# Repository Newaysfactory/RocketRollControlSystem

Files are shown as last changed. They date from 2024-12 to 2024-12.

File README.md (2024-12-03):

# RocketRollControlSystem
Repository containing code, documentation and other about my master's degree thesis about an aerodynamic roll control system for model rockets 

## Things to know before you start
* Main source of documentation is my degree thesis placed on the repository root folder.
* This source code and documentation is from 2012. It is provided essentially for educational purposes, since many of the hardware components used are obsolete today.
* Documentation and the master's degree thesis are mainly in italian.

## What you find here
* **Thesis_2.3.pdf** Start [here](https://github.com/Newaysfactory/RocketRollControlSystem/blob/036ea757c4abbbe03a6e53f3893280afd1d1502c/Thesis_2.3%20-%20Active%20roll%20control%20system%20for%20a%20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))  to understand this project
* **License** This project is under GNU General Public License v3.0
* **FlightTrialsLogbook** Logbook of the six experimental fligts I did with the roll control system
* **Electronics -> Firmware** The source code of the roll control system in C language. Open it with Microchip MPLAB IDE. Under "File per MPLAB Simulator" it also contains some stimuli file I used to test the system on bench
* **Electronics -> HardwareDesign** The PCB images (top and bottom) and the schematic and PCB source. To open in Labcenter Proteus ISIS and ARES. Further info in the local readme.txt
* **ExcelSheets** Some spreadsheets I used to dimension the control fins. Further info in the local readme.txt
* **Matlab** A couple of Simulink models I used to design the control system. Those closed loop models contains the mathematical model of the rocket, the actuator dynamics, the fins aerodynamics and the controller. Further info in the local readme.txt
* **Openrocket** The .ENG rocket motor thrust curves to be used with RockSim
* **PC Software** The source code in Visual Basic and the executable of the software I developed to setup the roll control system and to download flight data after the flight. Further info in the local readme.txt
* **Pictures** Pictures of all the building process
* **Rocket drawings** 3D CAD mechanical drawings of the rocket and of the control system in McNeel Rhinoceros format
* **RocksimModel** Rocksim model to simulate the rocket stability and simulate the flight

## Known issues and limitations:
* Roll angle, rate and acceleration in output from the roll Kalman fileter are not fully coherent. I never investigate further.

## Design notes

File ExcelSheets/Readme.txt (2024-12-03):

Folder content

Analisi dati di volo - Prova a terra per integrazione.xlsx
I did a ground recording moving the rocket and tried to replicate in excel the same integration algorithm is running on the microcontroller

Output Digital DATCOM.xlsx
Spreadsheet summarizing the output of the digital DATCOM fortran software for my control fins

Dimensionamento canard per tentativi.xlsm
Spreadsheet with a Macro to find the canard fins dimension given some input data 

Momento di cerniera.xlsx
A spreadsheet to calculate the hinge torque depending on the fin geometry, alpha (rocket angle of attack) and delta (fin deflection)

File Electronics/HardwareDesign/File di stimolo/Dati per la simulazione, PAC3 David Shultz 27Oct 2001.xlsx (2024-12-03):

*** Conf | iguration | ***
Trigger: | G-switch,
Smart Re | covery opt | ion enabl
Timed re | covery set | at 25 se
Data is | sampled at | 200 Hz
Inputs t | hat were s | ampled: A
This dat | a was gene | rated wit
and down | loaded fro | m an RDAS
 |  |  |  |  |  |  | 0 m/s^2 (V) = |  | 0 m = V0 = |  | 0 m/s^2 (V) = |  |  | 0 m = V0 =
*** Inte | rpreted da | ta *** |  |  |  |  | 2.41 |  | 4.085 |  | 1974.3 |  |  | 3346
Time | Acc [G] | Alt [ft] | Time | Acc [m/s^2] | Alt [m] | Time | Acc [V] | Time | Alt [V] | Time | Acc [ADC] |  | Time | Alt [ADC]
-2.000 | 1.10 | -7 | 0.000 | 10.791 | -2.1336 | 0.000 | 2.366 | 0.000 | 4.086212722 | 0.000 |  |  | 0.000 | 3347
-1.995 | 1.00 | -7 | 0.005 | 9.81 | -2.1336 | 0.005 | 2.37 | 0.005 | 4.086212722 | 0.005 |  |  | 0.005 | 3347
-1.990 | 1.00 | -7 | 0.010 | 9.81 | -2.1336 | 0.010 | 2.37 | 0.010 | 4.086212722 | 0.010 |  |  | 0.010 | 3347
-1.985 | 0.90 | 18 | 0.015 | 8.829 | 5.4864 | 0.015 | 2.374 | 0.015 | 4.081882785 | 0.015 |  |  | 0.015 | 3344
-1.980 | 1.00 | -7 | 0.020 | 9.81 | -2.1336 | 0.020 | 2.37 | 0.020 | 4.086212722 | 0.020 |  |  | 0.020 | 3347
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

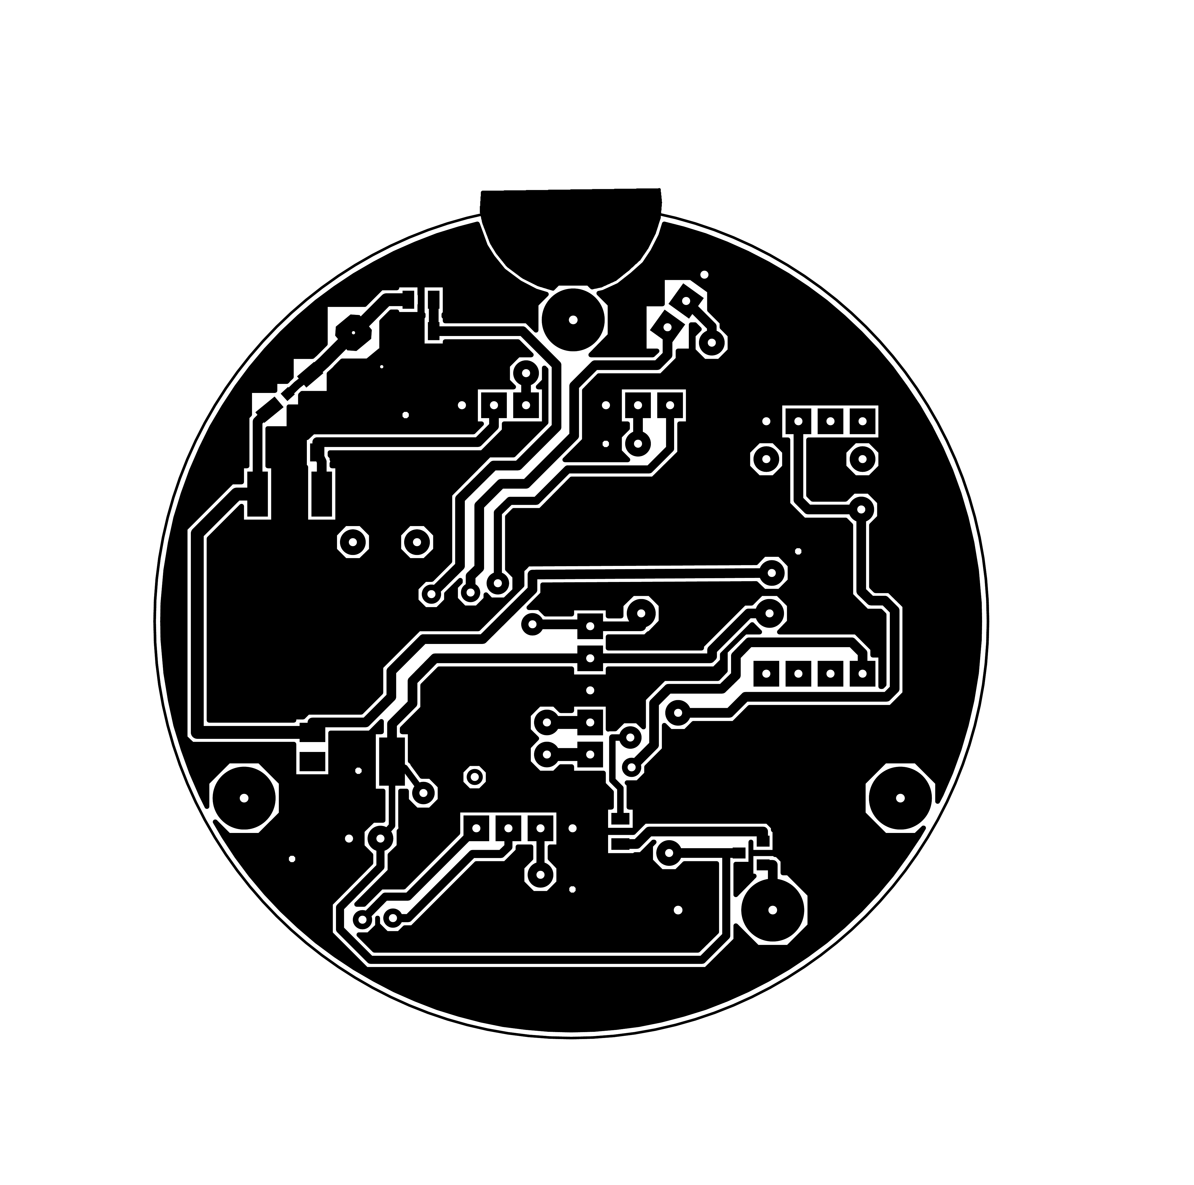
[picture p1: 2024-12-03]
Electronics/HardwareDesign/pcb scheda madre bottom.tif

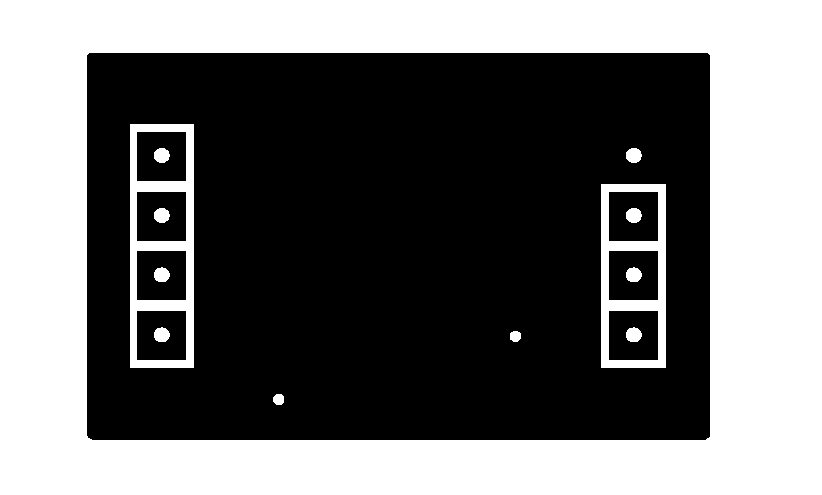
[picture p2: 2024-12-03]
Electronics/HardwareDesign/pcb gyro bottom.tif

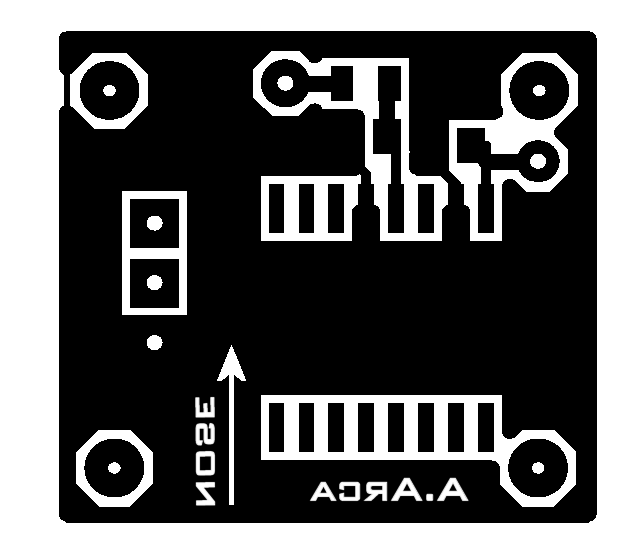
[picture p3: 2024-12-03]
Electronics/HardwareDesign/pcb accelerometro top.tif

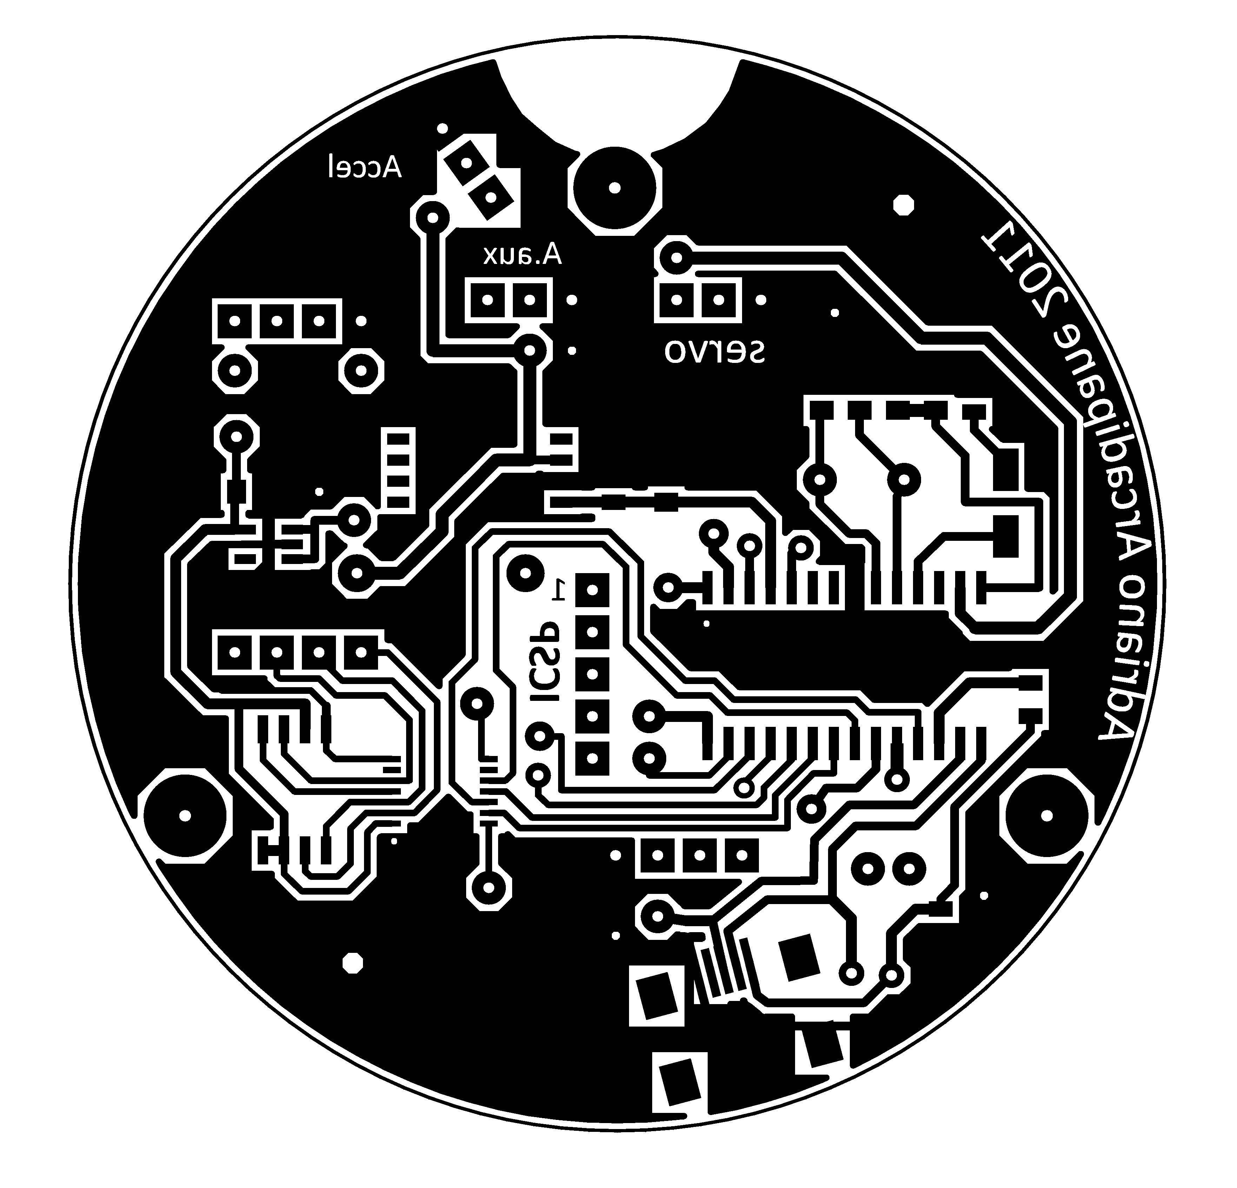
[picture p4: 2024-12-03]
Electronics/HardwareDesign/pcb scheda madre top.tif

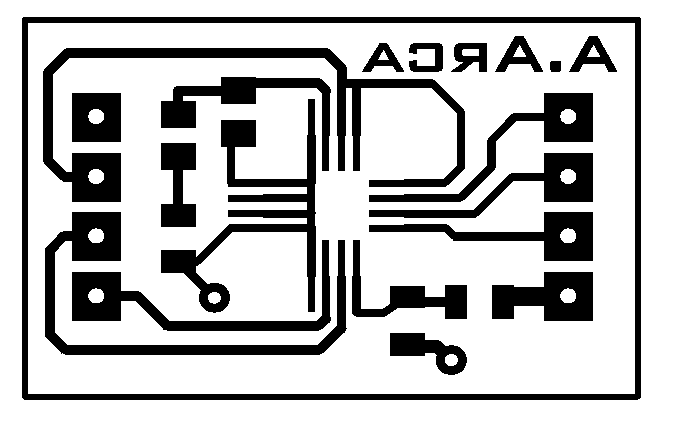
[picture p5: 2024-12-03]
Electronics/HardwareDesign/pcb gyro top.tif

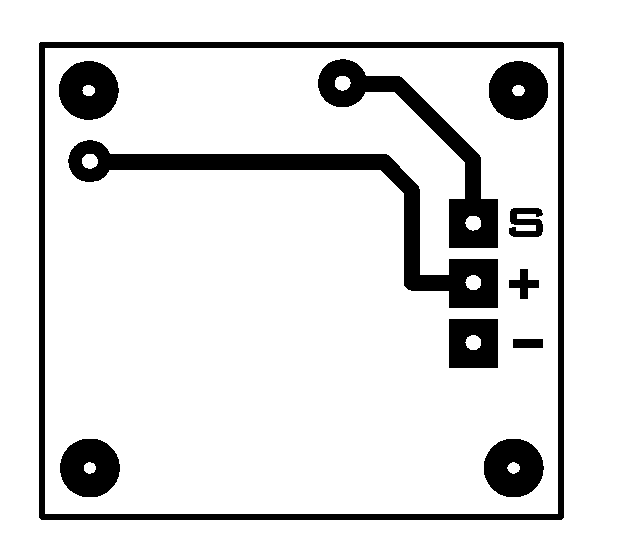
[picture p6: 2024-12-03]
Electronics/HardwareDesign/pcb accelerometro bottom.tif

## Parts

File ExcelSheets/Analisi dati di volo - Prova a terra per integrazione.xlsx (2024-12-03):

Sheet: Dati tabulari
 |  |  |  |  |  | Volo1 |  |  |  |  |  |  |  |  |  |  |  |  | Integrato con metodo dei trapezi
T | Acc | P | Aux | GyroX(-yaw) | GyroY(Pitch) | GYroZ(Roll) | Alt | Speed | Acc | Ang p | Ang speed | Ang acc | Servo pos | Yaw v (-X) | Pitch v (Y) | Roll v (Z) | Roll v (filtered) | pitch angle | Yaw angle | Roll angle | Roll angle (filtered)
[s] | [ADC] | [ADC] | [ADC] | [ADC] | [ADC] | [ADC] | [m] | [m/s] | [m/s^2] | [rad] | [rad/s] | [rad/s^2] | [rad] | [deg/s] | [deg/s] | [deg/s] | [deg/s] | [deg] | [deg] | [deg] | [deg]
0 | 2005 | 3325 | 3061 | 3 | 101 | 2832 | 0.4 | 9.14 | 11.24 | 0 | 0.378 | 0000,00 0,00000 |  | -0.0525 | 1.7675 | 49.9625 | 21.6594 | -0.0076125 | 0.0126875 | 0.5158125 | 0.2432385
0.01 | 2001 | 3324 | 3060 | 84 | 44 | 3017 | 0.55 | 9.3 | 11.27 | 0 | 0.471 | 0000,00 0,00000 |  | -1.47 | 0.77 | 53.2 | 26.9883 | -0.0102375 | 0.015575 | 1.0616375 | 0.539193
0.02 | 2002 | 3326 | 3060 | -54 | -11 | 3175 | 0.54 | 9.34 | 11.23 | 0 | 0.562 | 0000,00 0,00000 |  | 0.945 | -0.1925 | 55.965 | 32.2026 | -0.007875 | 0.0163625 | 1.6538375 | 0.889296
0.03 | 2003 | 3325 | 3062 | 27 | 20 | 3547 | 0.61 | 9.43 | 11.15 | 0 | 0.66 | 0000,00 0,00000 |  | -0.4725 | 0.35 | 62.475 | 37.818 | -0.0048125 | 0.0168875 | 2.32925 | 1.2998505
0.04 | 2006 | 3326 | 3059 | -62 | -14 | 4126 | 0.6 | 9.45 | 10.91 | 0 | 0.773 | 0000,00 0,00000 |  | 1.085 | -0.245 | 72.6075 | 44.2929 | -0.0051625 | 0.016275 | 3.078425 | 1.7748675
0.05 | 1998 | 3326 | 3061 | 66 | 7 | 4390 | 0.59 | 9.49 | 11.16 | 0 | 0.885 | 0000,00 0,00000 |  | -1.155 | 0.1225 | 77.2275 | 50.7105 | -0.015225 | 0.0114625 | 3.87345 | 2.314347
0.06 | 1996 | 3326 | 3059 | 49 | -62 | 4650 | 0.58 | 9.53 | 11.48 | 0 | 0.998 | 0000,00 0,00000 |  | -0.8575 | -1.085 | 81.7775 | 57.1854 | -0.0105875 | 0.0140875 | 4.6855375 | 2.9145645
0.07 | 1987 | 3326 | 3060 | -102 | 92 | 4585 | 0.58 | 9.6 | 12.25 | 0 | 1.097 | 0000,00 0,00000 |  | 1.785 | 1.61 | 80.64 | 62.8581 | 0.002975 | -0.0037625 | 5.0033375 | 3.504468
0.08 | 2006 | 3326 | 3060 | -53 | -296 | -999 | 0.57 | 9.62 | 11.8 | 0 | 0.962 | 0000,00 0,00000 |  | 0.9275 | -5.18 | -17.08 | 55.1226 | 0.0090125 | -0.0546875 | 4.9116375 | 4.028763
0.09 | 2002 | 3326 | 3060 | -16 | -286 | -95 | 0.56 | 9.66 | 11.67 | 0 | 0.868 | 0000,00 0,00000 |  | 0.28 | -5.005 | -1.26 | 49.7364 | 0.0126 | -0.071575 | 4.902275 | 4.5012015
0.1 | 1998 | 3326 | 3061 | -25 | 93 | -58 | 0.56 | 9.7 | 11.78 | 0 | 0.781 | 0000,00 0,00000 |  | 0.4375 | 1.6275 | -0.6125 | 44.7513 | 0.014175 | -0.0441 | 4.8580875 | 4.919778
0.11 | 2000 | 3326 | 3061 | 7 | 221 | -493 | 0.55 | 9.74 | 11.76 | 0 | 0.68 | 0000,00 0,00000 |  | -0.1225 | 3.8675 | -8.225 | 38.964 | 0.014875 | -0.01295 | 4.78555 | 5.2833465
0.12 | 1998 | 3326 | 3060 | -15 | 135 | -382 | 0.55 | 9.78 | 11.86 | 0 | 0.589 | 0000,00 0,00000 |  | 0.2625 | 2.3625 | -6.2825 | 33.7497 | 0.0216125 | 0.006475 | 4.72885 | 5.597064
0.13 | 2003 | 3325 | 3060 | -62 | 87 | -312 | 0.62 | 9.87 | 11.65 | 0 | 0.506 | 0000,00 0,00000 |  | 1.085 | 1.5225 | -5.0575 | 28.9938 | 0.02905 | 0.02065 | 4.6834375 | 5.8655145
0.14 | 2001 | 3324 | 3060 | -23 | 75 | -253 | 0.77 | 10.02 | 11.6 | 0 | 0.431 | 0000,00 0,00000 |  | 0.4025 | 1.3125 | -4.025 | 24.6963 | 0.0329 | 0.029225 | 4.63925 | 6.092136
0.15 | 2004 | 3326 | 3062 | -21 | 23 | -298 | 0.76 | 10.04 | 11.39 | 0 | 0.36 | 0000,00 0,00000 |  | 0.3675 | 0.4025 | -4.8125 | 20.628 | 0.0373625 | 0.0305375 | 4.601975 | 6.2809395
0.16 | 2007 | 3326 | 3060 | -30 | -8 | -174 | 0.75 | 10.06 | 11.05 | 0 | 0.299 | 0000,00 0,00000 |  | 0.525 | -0.14 | -2.6425 | 17.1327 | 0.041825 | 0.03115 | 4.5878875 | 6.437655
0.17 | 2006 | 3326 | 3061 | -21 | 15 | -33 | 0.74 | 10.07 | 10.83 | 0 | 0.248 | 0000,00 0,00000 |  | 0.3675 | 0.2625 | -0.175 | 14.2104 | 0.049 | 0.041475 | 4.6004 | 6.5685855
0.18 | 2000 | 3326 | 3061 | -61 | 103 | 130 | 0.73 | 10.1 | 10.99 | 0 | 0.209 | 0000,00 0,00000 |  | 1.0675 | 1.8025 | 2.6775 | 11.9757 | 0.05845 | 0.056 | 4.6249875 | 6.677742
0.19 | 2002 | 3326 | 3060 | -47 | 63 | 105 | 0.72 | 10.13 | 11.01 | 0 | 0.172 | 0000,00 0,00000 |  | 0.8225 | 1.1025 | 2.24 | 9.8556 | 0.065625 | 0.0630875 | 4.629975 | 6.764265
0.2 | 2004 | 3326 | 3060 | -35 | 18 | -94 | 0.72 | 10.15 | 10.91 | 0 | 0.13 | 0000,00 0,00000 |  | 0.6125 | 0.315 | -1.2425 | 7.449 | 0.0748125 | 0.0681625 | 4.6118625 | 6.8275815
0.21 | 2000 | 3326 | 3062 | -70 | 40 | -159 | 0.71 | 10.18 | 11.05 | 0 | 0.091 | 0000,00 0,00000 |  | 1.225 | 0.7 | -2.38 | 5.2143 | 0.085925 | 0.0721 | 4.5801 | 6.8682645
0.22 | 1996 | 3325 | 3060 | -57 | 5 | -250 | 0.78 | 10.29 | 11.39 | 0 | 0.051 | 0000,00 0,00000 |  | 0.9975 | 0.0875 | -3.9725 | 2.9223 | 0.0916125 | 0.0595 | 4.521475 | 6.8848815
0.23 | 2003 | 3326 | 3061 | -8 | -149 | -466 | 0.78 | 10.31 | 11.28 | 0 | 0.007 | 0000,00 0,00000 |  | 0.14 | -2.6075 | -7.7525 | 0.4011 | 0.0916125 | 0.0392 | 4.4366875 | 6.876573
0.24 | 2006 | 3326 | 3061 | 8 | -83 | -549 | 0.77 | 10.32 | 11.01 | 0 | -0.036 | 0000,00 0,00000 |  | -0.14 | -1.4525 | -9.205 | -2.0628 | 0.0973875 | 0.0347375 | 4.3267875 | 6.8424795
0.25 | 2001 | 3326 | 3062 | -74 | 32 | -753 | 0.76 | 10.35 | 11.08 | 0 | -0.083 | 0000,00 0,00000 |  | 1.295 | 0.56 | -12.775 | -4.7559 | 0.113225 | 0.0403375 | 4.1890625 | 6.7817415
0.26 | 2003 | 3326 | 3061 | -107 | 32 | -867 | 0.75 | 10.37 | 11.02 | 0 | -0.129 | 0000,00 0,00000 |  | 1.8725 | 0.56 | -14.77 | -7.3917 | 0.13195 | 0.0594125 | 4.05685 | 6.6980835
0.27 | 2004 | 3326 | 3060 | -107 | 186 | -690 | 0.75 | 10.39 | 10.92 | 0 | -0.163 | 0000,00 0,00000 |  | 1.8725 | 3.255 | -11.6725 | -9.3399 | 0.15015 | 0.0695625 | 3.909325 | 6.5920785
0.28 | 1997 | 3326 | 3060 | -101 | -70 | -1042 | 0.74 | 10.43 | 11.23 | 0 | -0.207 | 0000,00 0,00000 |  | 1.7675 | -1.225 | -17.8325 | -11.8611 | 0.166425 | 0.1085875 | 3.7046625 | 6.4585695
0.29 | 1998 | 3326 | 3062 | -85 | 516 | -1343 | 0.74 | 10.47 | 11.43 | 0 | -0.259 | 0000,00 0,00000 |  | 1.4875 | 9.03 | -23.1 | -14.8407 | 0.1903125 | 0.167475 | 3.4503875 | 6.293832
0.3 | 2000 | 3326 | 3060 | -188 | 157 | -1609 | 0.73 | 10.5 | 11.47 | 0 | -0.316 | 0000,00 0,00000 |  | 3.29 | 2.7475 | -27.755 | -18.1068 | 0.2249625 | 0.1966125 | 3.11325 | 6.090417
0.31 | 2000 | 3326 | 3062 | -208 | 176 | -2290 | 0.73 | 10.53 | 11.51 | 0 | -0.394 | 0000,00 0,00000 |  | 3.64 | 3.08 | -39.6725 | -22.5762 | 0.24745 | 0.2037 | 2.7493375 | 5.848611
0.32 | 1995 | 3326 | 3062 | -49 | -95 | -1915 | 0.73 | 10.58 | 11.82 | 0 | -0.45 | 0000,00 0,00000 |  | 0.8575 | -1.6625 | -33.11 | -25.785 | 0.24605 | 0.1833125 | 2.4075625 | 5.57529
0.33 | 2002 | 3326 | 3061 | 65 | -138 | -2037 | 0.72 | 10.61 | 11.68 | 0 | -0.504 | 0000,00 0,00000 |  | -1.1375 | -2.415 | -35.245 | -28.8792 | 0.243075 | 0.1399125 | 2.0804 | 5.276184
0.34 | 2007 | 3326 | 3060 | -31 | -358 | -1748 | 0.72 | 10.62 | 11.29 | 0 | -0.54 | 0000,00 0,00000 |  | 0.5425 | -6.265 | -30.1875 | -30.942 | 0.2513875 | 0.056 | 1.785175 | 4.9584555
0.35 | 2006 | 3326 | 3061 | -64 | -601 | -1672 | 0.71 | 10.64 | 11.02 | 0 | -0.569 | 0000,00 0,00000 |  | 1.12 | -10.5175 | -28.8575 | -32.6037 | 0.270025 | 0.020825 | 1.5206625 | 4.628694
0.36 | 2004 | 3326 | 3062 | -149 | 199 | -1397 | 0.71 | 10.66 | 10.92 | 0 | -0.582 | 0000,00 0,00000 |  | 2.6075 | 3.4825 | -24.045 | -33.3486 | 0.2874375 | 0.059325 | 1.2840625 | 4.292916
0.37 | 1993 | 3326 | 3060 | -50 | 241 | -1353 | 0.71 | 10.71 | 11.45 | 0 | -0.59 | 0000,00 0,00000 |  | 0.875 | 4.2175 | -23.275 | -33.807 | 0.3016125 | 0.100275 | 1.1053875 | 3.960576
0.38 | 2004 | 3326 | 3062 | -112 | 227 | -735 | 0.71 | 10.73 | 11.27 | 0 | -0.57 | 0000,00 0,00000 |  | 1.96 | 3.9725 | -12.46 | -32.661 | 0.3254125 | 0.1514625 | 1.03565 | 3.6468585
0.39 | 2000 | 3326 | 3060 | -160 | 358 | -108 | 0.71 | 10.76 | 11.35 | 0 | -0.525 | 0000,00 0,00000 |  | 2.8 | 6.265 | -1.4875 | -30.0825 | 0.353675 | 0.21455 | 1.05805 | 3.3637965
0.4 | 2002 | 3326 | 3060 | -163 | 363 | 318 | 0.71 | 10.79 | 11.3 | 0 | -0.463 | 0000,00 0,00000 |  | 2.8525 | 6.3525 | 5.9675 | -26.5299 | 0.38395 | 0.2800875 | 1.130325 | 3.1168335
0.41 | 2002 | 3326 | 3058 | -183 | 386 | 462 | 0.71 | 10.82 | 11.25 | 0 | -0.399 | 0000,00 0,00000 |  | 3.2025 | 6.755 | 8.4875 | -22.8627 | 0.4076625 | 0.3325875 | 1.2004125 | 2.9036775
0.42 | 2000 | 3326 | 3060 | -88 | 214 | 293 | 0.71 | 10.85 | 11.33 | 0 | -0.345 | 0000,00 0,00000 |  | 1.54 | 3.745 | 5.53 | -19.7685 | 0.41545 | 0.3462375 | 1.227975 | 2.717166
0.43 | 2004 | 3326 | 3060 | -1 | -58 | -24 | 0.71 | 10.87 | 11.17 | 0 | -0.306 | 0000,00 0,00000 |  | 0.0175 | -1.015 | -0.0175 | -17.5338 | 0.4186875 | 0.33565 | 1.227625 | 2.552142
0.44 | 2004 | 3326 | 3062 | -36 | -63 | -26 | 0.7 | 10.89 | 11.04 | 0 | -0.27 | 0000,00 0,00000 |  | 0.63 | -1.1025 | -0.0525 | -15.471 | 0.4276125 | 0.3350375 | 1.23515 | 2.408319
0.45 | 2002 | 3326 | 3062 | -66 | 56 | 66 | 0.71 | 10.92 | 11.05 | 0 | -0.232 | 0000,00 0,00000 |  | 1.155 | 0.98 | 1.5575 | -13.2936 | 0.4391625 | 0.3423875 | 1.247575 | 2.2848375
0.46 | 1999 | 3326 | 3062 | -66 | 28 | 30 | 0.71 | 10.95 | 11.22 | 0 | -0.199 | 0000,00 0,00000 |  | 1.155 | 0.49 | 0.9275 | -11.4027 | 0.451325 | 0.345625 | 1.2525625 | 2.1794055
0.47 | 2000 | 3326 | 3061 | -73 | 9 | -19 | 0.71 | 10.98 | 11.31 | 0 | -0.169 | 0000,00 0,00000 |  | 1.2775 | 0.1575 | 0.07 | -9.6837 | 0.4662875 | 0.3548125 | 1.2595625 | 2.090877
0.48 | 2002 | 3325 | 3062 | -98 | 96 | 53 | 0.79 | 11.07 | 11.26 | 0 | -0.14 | 0000,00 0,00000 |  | 1.715 | 1.68 | 1.33 | -8.022 | 0.476525 | 0.3679375 | 1.2662125 | 2.0178195
0.49 | 2002 | 3326 | 3060 | -19 | 54 | -23 | 0.79 | 11.1 | 11.23 | 0 | -0.115 | 0000,00 0,00000 |  | 0.3325 | 0.945 | 0 | -6.5895 | 0.47985 | 0.376775 | 1.267 | 1.958514
0.5 | 2002 | 3326 | 3062 | -19 | 47 | -14 | 0.79 | 11.12 | 11.2 | 0 | -0.092 | 0000,00 0,00000 |  | 0.3325 | 0.8225 | 0.1575 | -5.2716 | 0.484575 | 0.3808 | 1.2691 | 1.911528
0.51 | 1999 | 3326 | 3060 | -35 | -1 | -8 | 0.79 | 11.15 | 11.34 | 0 | -0.072 | 0000,00 0,00000 |  | 0.6125 | -0.0175 | 0.2625 | -4.1256 | 0.4914 | 0.3824625 | 1.2718125 | 1.8757155
0.52 | 2006 | 3326 | 3062 | -43 | 20 | -7 | 0.79 | 11.17 | 11.07 | 0 | -0.053 | 0000,00 0,00000 |  | 0.7525 | 0.35 | 0.28 | -3.0369 | 0.4986625 | 0.3868375 | 1.272425 | 1.8499305
0.53 | 1999 | 3326 | 3061 | -40 | 30 | -32 | 0.79 | 11.2 | 11.24 | 0 | -0.037 | 0000,00 0,00000 |  | 0.7 | 0.525 | -0.1575 | -2.1201 | 0.504875 | 0.3927 | 1.270325 | 1.8327405
0.54 | 2003 | 3326 | 3062 | -31 | 37 | -38 | 0.79 | 11.22 | 11.15 | 0 | -0.023 | 0000,00 0,00000 |  | 0.5425 | 0.6475 | -0.2625 | -1.3179 | 0.5130125 | 0.4011 | 1.2700625 | 1.823286
0.55 | 2001 | 3326 | 3062 | -62 | 59 | -11 | 0.79 | 11.25 | 11.19 | 0 | -0.01 | 0000,00 0,00000 |  | 1.085 | 1.0325 | 0.21 | -0.573 | 0.5210625 | 0.4106375 | 1.2726 | 1.820994
0.56 | 2009 | 3326 | 3060 | -30 | 50 | -6 | 0.79 | 11.26 | 10.78 | 0 | 0.002 | 0000,00 0,00000 |  | 0.525 | 0.875 | 0.2975 | 0.1146 | 0.5284125 | 0.420875 | 1.2751375 | 1.8252915
0.57 | 2006 | 3326 | 3061 | -54 | 67 | -11 | 0.79 | 11.27 | 10.61 | 0 | 0.013 | 0000,00 0,00000 |  | 0.945 | 1.1725 | 0.21 | 0.7449 | 0.53865 | 0.4284 | 1.2786375 | 1.835319
0.58 | 2002 | 3325 | 3060 | -63 | 19 | 5 | 0.87 | 11.35 | 10.7 | 0 | 0.022 | 0000,00 0,00000 |  | 1.1025 | 0.3325 | 0.49 | 1.2606 | 0.5488 | 0.43365 | 1.2847625 | 1.8505035
0.59 | 2004 | 3325 | 3060 | -53 | 41 | 19 | 0.95 | 11.43 | 10.66 | 0 | 0.031 | 0000,00 0,00000 |  | 0.9275 | 0.7175 | 0.735 | 1.7763 | 0.5586875 | 0.4409125 | 1.2915 | 1.870272
0.6 | 1998 | 3326 | 3060 | -60 | 42 | 12 | 0.94 | 11.46 | 10.96 | 0 | 0.038 | 0000,00 0,00000 |  | 1.05 | 0.735 | 0.6125 | 2.1774 | 0.5679625 | 0.447825 | 1.2971 | 1.8934785
0.61 | 2003 | 3326 | 3060 | -46 | 37 | 6 | 0.94 | 11.48 | 10.92 | 0 | 0.043 | 0000,00 0,00000 |  | 0.805 | 0.6475 | 0.5075 | 2.4639 | 0.5768875 | 0.4545625 | 1.302 | 1.91955
0.62 | 2008 | 3326 | 3060 | -56 | 40 | 4 | 0.94 | 11.48 | 10.62 | 0 | 0.048 | 0000,00 0,00000 |  | 0.98 | 0.7 | 0.4725 | 2.7504 | 0.5873 | 0.4610375 | 1.30585 | 1.9479135
0.63 | 2002 | 3326 | 3060 | -63 | 34 | -6 | 0.94 | 11.5 | 10.7 | 0 | 0.051 | 0000,00 0,00000 |  | 1.1025 | 0.595 | 0.2975 | 2.9223 | 0.5964875 | 0.4666375 | 1.31075 | 1.977996
0.64 | 2014 | 3326 | 3062 | -42 | 30 | 16 | 0.93 | 11.49 | 10.1 | 0 | 0.054 | 0000,00 0,00000 |  | 0.735 | 0.525 | 0.6825 | 3.0942 | 0.6054125 | 0.472325 | 1.31425 | 2.0092245
0.65 | 2008 | 3326 | 3060 | -60 | 35 | -22 | 0.93 | 11.49 | 9.95 | 0 | 0.055 | 0000,00 0,00000 |  | 1.05 | 0.6125 | 0.0175 | 3.1515 | 0.6115375 | 0.4804625 | 1.3162625 | 2.0413125
0.66 | 2003 | 3327 | 3062 | -10 | 58 | -1 | 0.85 | 11.45 | 10.1 | 0 | 0.057 | 0000,00 0,00000 |  | 0.175 | 1.015 | 0.385 | 3.2661 | 0.617225 | 0.48685 | 1.3194125 | 2.0739735
0.67 | 2003 | 3326 | 3061 | -55 | 15 | -9 | 0.85 | 11.47 | 10.23 | 0 | 0.057 | 0000,00 0,00000 |  | 0.9625 | 0.2625 | 0.245 | 3.2661 | 0.624575 | 0.490525 | 1.3223 | 2.1066345
0.68 | 2005 | 3326 | 3062 | -29 | 27 | -4 | 0.85 | 11.48 | 10.22 | 0 | 0.057 | 0000,00 0,00000 |  | 0.5075 | 0.4725 | 0.3325 | 3.2661 | 0.6313125 | 0.4946375 | 1.3225625 | 2.1387225
0.69 | 2008 | 3326 | 3061 | -48 | 20 | -39 | 0.85 | 11.49 | 10.04 | 0 | 0.055 | 0000,00 0,00000 |  | 0.84 | 0.35 | -0.28 | 3.1515 | 0.636475 | 0.498575 | 1.3223 | 2.169951
0.7 | 2006 | 3326 | 3061 | -11 | 25 | -10 | 0.85 | 11.5 | 10.01 | 0 | 0.054 | 0000,00 0,00000 |  | 0.1925 | 0.4375 | 0.2275 | 3.0942 | 0.6412875 | 0.50225 | 1.3243125 | 2.20032
0.71 | 2003 | 3326 | 3062 | -44 | 17 | -13 | 0.85 | 11.52 | 10.15 | 0 | 0.052 | 0000,00 0,00000 |  | 0.77 | 0.2975 | 0.175 | 2.9796 | 0.648725 | 0.5061875 | 1.3251 | 2.229543
0.72 | 2003 | 3326 | 3060 | -41 | 28 | -24 | 0.85 | 11.53 | 10.27 | 0 | 0.05 | 0000,00 0,00000 |  | 0.7175 | 0.49 | -0.0175 | 2.865 | 0.65555 | 0.512225 | 1.3237875 | 2.2573335
0.73 | 2000 | 3326 | 3061 | -37 | 41 | -37 | 0.86 | 11.56 | 10.53 | 0 | 0.047 | 0000,00 0,00000 |  | 0.6475 | 0.7175 | -0.245 | 2.6931 | 0.6633375 | 0.5172125 | 1.3225625 | 2.2836915
0.74 | 2002 | 3326 | 3060 | -52 | 16 | -23 | 0.86 | 11.58 | 10.63 | 0 | 0.045 | 0000,00 0,00000 |  | 0.91 | 0.28 | 0 | 2.5785 | 0.6689375 | 0.519575 | 1.3225625 | 2.308617
0.75 | 2006 | 3326 | 3062 | -12 | 11 | -23 | 0.86 | 11.59 | 10.49 | 0 | 0.042 | 0000,00 0,00000 |  | 0.21 | 0.1925 | 0 | 2.4066 | 0.67095 | 0.5235125 | 1.3230875 | 2.33211
0.76 | 2003 | 3326 | 3062 | -11 | 34 | -17 | 0.86 | 11.61 | 10.55 | 0 | 0.04 | 0000,00 0,00000 |  | 0.1925 | 0.595 | 0.105 | 2.292 | 0.6748 | 0.5264 | 1.323875 | 2.354457
0.77 | 2006 | 3326 | 3061 | -33 | -1 | -20 | 0.86 | 11.62 | 10.42 | 0 | 0.038 | 0000,00 0,00000 |  | 0.5775 | -0.0175 | 0.0525 | 2.1774 | 0.6796125 | 0.5292 | 1.322475 | 2.375085
0.78 | 2010 | 3325 | 3062 | -22 | 33 | -42 | 0.94 | 11.68 | 10.1 | 0 | 0.034 | 0000,00 0,00000 |  | 0.385 | 0.5775 | -0.3325 | 1.9482 | 0.6867 | 0.5345375 | 1.3188 | 2.3937075
0.79 | 2004 | 3325 | 3060 | -59 | 28 | -46 | 1.02 | 11.76 | 10.17 | 0 | 0.031 | 0000,00 0,00000 |  | 1.0325 | 0.49 | -0.4025 | 1.7763 | 0.6916875 | 0.539 | 1.3194125 | 2.411184
0.8 | 1999 | 3326 | 3060 | 2 | 23 | 7 | 1.02 | 11.78 | 10.5 | 0 | 0.03 | 0000,00 0,00000 |  | -0.035 | 0.4025 | 0.525 | 1.719 | 0.69405 | 0.544425 | 1.321775 | 2.4275145
0.81 | 1999 | 3326 | 3060 | -29 | 39 | -26 | 1.02 | 11.81 | 10.78 | 0 | 0.027 | 0000,00 0,00000 |  | 0.5075 | 0.6825 | -0.0525 | 1.5471 | 0.6986875 | 0.5506375 | 1.3211625 | 2.4424125
0.82 | 1999 | 3326 | 3061 | -24 | 32 | -27 | 1.02 | 11.83 | 11 | 0 | 0.025 | 0000,00 0,00000 |  | 0.42 | 0.56 | -0.07 | 1.4325 | 0.7025375 | 0.5555375 | 1.3213375 | 2.4561645
0.83 | 2001 | 3326 | 3062 | -20 | 24 | -17 | 1.01 | 11.85 | 11.07 | 0 | 0.023 | 0000,00 0,00000 |  | 0.35 | 0.42 | 0.105 | 1.3179 | 0.70875 | 0.5607 | 1.3223 | 2.4687705
0.84 | 2004 | 3326 | 3062 | -51 | 35 | -18 | 1.01 | 11.87 | 10.96 | 0 | 0.021 | 0000,00 0,00000 |  | 0.8925 | 0.6125 | 0.0875 | 1.2033 | 0.716975 | 0.568225 | 1.322475 | 2.4802305
0.85 | 2006 | 3326 | 3060 | -43 | 51 | -26 | 1.01 | 11.87 | 10.76 | 0 | 0.019 | 0000,00 0,00000 |  | 0.7525 | 0.8925 | -0.0525 | 1.0887 | 0.723275 | 0.5758375 | 1.3220375 | 2.4905445
0.86 | 2006 | 3326 | 3060 | -29 | 36 | -25 | 1.01 | 11.88 | 10.59 | 0 | 0.017 | 0000,00 0,00000 |  | 0.5075 | 0.63 | -0.035 | 0.9741 | 0.728175 | 0.582575 | 1.3243125 | 2.499999
0.87 | 2003 | 3326 | 3062 | -27 | 41 | 5 | 1.01 | 11.9 | 10.63 | 0 | 0.016 | 0000,00 0,00000 |  | 0.4725 | 0.7175 | 0.49 | 0.9168 | 0.7342125 | 0.589225 | 1.3248375 | 2.508594
0.88 | 2002 | 3326 | 3060 | -42 | 35 | -45 | 1.01 | 11.91 | 10.71 | 0 | 0.014 | 0000,00 0,00000 |  | 0.735 | 0.6125 | -0.385 | 0.8022 | 0.744275 | 0.5957 | 1.3237 | 2.516043
0.89 | 2006 | 3326 | 3062 | -73 | 39 | -14 | 1.01 | 11.92 | 10.56 | 0 | 0.012 | 0000,00 0,00000 |  | 1.2775 | 0.6825 | 0.1575 | 0.6876 | 0.7581875 | 0.60375 | 1.3237875 | 2.5226325
0.9 | 2002 | 3325 | 3062 | -86 | 53 | -31 | 1.08 | 12 | 10.65 | 0 | 0.011 | 0000,00 0,00000 |  | 1.505 | 0.9275 | -0.14 | 0.6303 | 0.7709625 | 0.61285 | 1.32545 | 2.528649
0.91 | 2002 | 3326 | 3060 | -60 | 51 | 4 | 1.08 | 12.01 | 10.73 | 0 | 0.01 | 0000,00 0,00000 |  | 1.05 | 0.8925 | 0.4725 | 0.573 | 0.7847875 | 0.623175 | 1.3321875 | 2.5346655
0.92 | 1998 | 3326 | 3060 | -98 | 67 | 27 | 1.08 | 12.04 | 11.02 | 0 | 0.011 | 0000,00 0,00000 |  | 1.715 | 1.1725 | 0.875 | 0.6303 | 0.80045 | 0.6342 | 1.3393625 | 2.5409685
0.93 | 2001 | 3326 | 3060 | -81 | 59 | 9 | 1.08 | 12.06 | 11.09 | 0 | 0.011 | 0000,00 0,00000 |  | 1.4175 | 1.0325 | 0.56 | 0.6303 | 0.813925 | 0.645575 | 1.3482 | 2.547558
0.94 | 2000 | 3326 | 3060 | -73 | 71 | 46 | 1.08 | 12.08 | 11.2 | 0 | 0.012 | 0000,00 0,00000 |  | 1.2775 | 1.2425 | 1.2075 | 0.6876 | 0.828625 | 0.6570375 | 1.3573875 | 2.5547205
0.95 | 1999 | 3326 | 3060 | -95 | 60 | 13 | 1.08 | 12.1 | 11.34 | 0 | 0.013 | 0000,00 0,00000 |  | 1.6625 | 1.05 | 0.63 | 0.7449 | 0.8432375 | 0.6687625 | 1.3628125 | 2.561883
0.96 | 1996 | 3326 | 3060 | -72 | 74 | 3 | 1.08 | 12.14 | 11.63 | 0 | 0.012 | 0000,00 0,00000 |  | 1.26 | 1.295 | 0.455 | 0.6876 | 0.8591625 | 0.6815375 | 1.3670125 | 2.568759
0.97 | 2003 | 3326 | 3060 | -110 | 72 | -1 | 1.07 | 12.15 | 11.47 | 0 | 0.012 | 0000,00 0,00000 |  | 1.925 | 1.26 | 0.385 | 0.6876 | 0.8754375 | 0.6925625 | 1.3706 | 2.5753485
0.98 | 2003 | 3324 | 3062 | -76 | 54 | -4 | 1.23 | 12.29 | 11.34 | 0 | 0.011 | 0000,00 0,00000 |  | 1.33 | 0.945 | 0.3325 | 0.6303 | 0.8876875 | 0.702275 | 1.3741875 | 2.5816515
0.99 | 2005 | 3326 | 3061 | -64 | 57 | -1 | 1.22 | 12.29 | 11.12 | 0 | 0.011 | 0000,00 0,00000 |  | 1.12 | 0.9975 | 0.385 | 0.6303 | 0.9002 | 0.710325 | 1.377425 | 2.587668
1 | 2001 | 3326 | 3061 | -79 | 35 | -8 | 1.22 | 12.3 | 11.17 | 0 | 0.01 | 0000,00 0,00000 |  | 1.3825 | 0.6125 | 0.2625 | 0.573 | 0.9107 | 0.718375 | 1.379875 | 2.5931115
1.01 | 2008 | 3326 | 3061 | -41 | 57 | -10 | 1.21 | 12.3 | 10.82 | 0 | 0.009 | 0000,00 0,00000 |  | 0.7175 | 0.9975 | 0.2275 | 0.5157 | 0.920325 | 0.7287875 | 1.3815375 | 2.597982
1.02 | 2002 | 3326 | 3060 | -69 | 62 | -17 | 1.21 | 12.31 | 10.86 | 0 | 0.008 | 0000,00 0,00000 |  | 1.2075 | 1.085 | 0.105 | 0.4584 | 0.9321375 | 0.7382375 | 1.362725 | 2.599701
1.03 | 2004 | 3325 | 3061 | -66 | 46 | -244 | 1.28 | 12.38 | 10.79 | 0 | -0.002 | 0000,00 0,00000 |  | 1.155 | 0.805 | -3.8675 | -0.1146 | 0.9452625 | 0.7454125 | 1.365875 | 2.60142
1.04 | 2001 | 3326 | 3060 | -84 | 36 | 234 | 1.28 | 12.39 | 10.9 | 0 | 0.008 | 0000,00 0,00000 |  | 1.47 | 0.63 | 4.4975 | 0.4584 | 0.9578625 | 0.7513625 | 1.391425 | 2.6062905
1.05 | 2003 | 3326 | 3060 | -60 | 32 | 12 | 1.27 | 12.4 | 10.88 | 0 | 0.009 | 0000,00 0,00000 |  | 1.05 | 0.56 | 0.6125 | 0.5157 | 0.9688 | 0.758625 | 1.3936125 | 2.6108745
1.06 | 1998 | 3326 | 3060 | -65 | 51 | -33 | 1.27 | 12.42 | 11.14 | 0 | 0.007 | 0000,00 0,00000 |  | 1.1375 | 0.8925 | -0.175 | 0.4011 | 0.9772875 | 0.7646625 | 1.3936125 | 2.6148855
1.07 | 2008 | 3326 | 3060 | -32 | 18 | -13 | 1.26 | 12.41 | 10.79 | 0 | 0.007 | 0000,00 0,00000 |  | 0.56 | 0.315 | 0.175 | 0.4011 | 0.9849875 | 0.7692125 | 1.39475 | 2.61861
1.08 | 2002 | 3327 | 3060 | -56 | 34 | -20 | 1.18 | 12.36 | 10.84 | 0 | 0.006 | 0000,00 0,00000 |  | 0.98 | 0.595 | 0.0525 | 0.3438 | 0.9926875 | 0.7728 | 1.3960625 | 2.622048
1.09 | 2000 | 3326 | 3060 | -32 | 7 | -11 | 1.17 | 12.38 | 11 | 0 | 0.006 | 0000,00 0,00000 |  | 0.56 | 0.1225 | 0.21 | 0.3438 | 0.9989875 | 0.7762125 | 1.3974625 | 2.6251995
1.1 | 2004 | 3326 | 3061 | -40 | 32 | -19 | 1.17 | 12.39 | 10.9 | 0 | 0.005 | 0000,00 0,00000 |  | 0.7 | 0.56 | 0.07 | 0.2865 | 1.0066 | 0.7812875 | 1.397725 | 2.6280645
1.11 | 2001 | 3326 | 3060 | -47 | 26 | -24 | 1.17 | 12.41 | 10.99 | 0 | 0.005 | 0000,00 0,00000 |  | 0.8225 | 0.455 | -0.0175 | 0.2865 | 1.01325 | 0.7853125 | 1.3992125 | 2.6309295
1.12 | 2002 | 3325 | 3062 | -29 | 20 | -5 | 1.25 | 12.48 | 11.01 | 0 | 0.005 | 0000,00 0,00000 |  | 0.5075 | 0.35 | 0.315 | 0.2865 | 1.019725 | 0.78925 | 1.3999125 | 2.633508
1.13 | 2000 | 3326 | 3062 | -45 | 25 | -33 | 1.24 | 12.5 | 11.13 | 0 | 0.004 | 0000,00 0,00000 |  | 0.7875 | 0.4375 | -0.175 | 0.2292 | 1.0262875 | 0.79275 | 1.399475 | 2.6355135
1.14 | 2001 | 3326 | 3062 | -30 | 15 | -18 | 1.24 | 12.51 | 11.18 | 0 | 0.003 | 0000,00 0,00000 |  | 0.525 | 0.2625 | 0.0875 | 0.1719 | 1.0311875 | 0.796075 | 1.398425 | 2.636946
1.15 | 2006 | 3326 | 3062 | -26 | 23 | -40 | 1.24 | 12.51 | 10.93 | 0 | 0.002 | 0000,00 0,00000 |  | 0.455 | 0.4025 | -0.2975 | 0.1146 | 1.036 | 0.79975 | 1.3976375 | 2.638092
1.16 | 2001 | 3326 | 3062 | -29 | 19 | -15 | 1.23 | 12.52 | 11.02 | 0 | 0.002 | 0000,00 0,00000 |  | 0.5075 | 0.3325 | 0.14 | 0.1146 | 1.041075 | 0.802375 | 1.4014875 | 2.6395245
1.17 | 2002 | 3328 | 3061 | -29 | 11 | 13 | 1.07 | 12.41 | 11.03 | 0 | 0.003 | 0000,00 0,00000 |  | 0.5075 | 0.1925 | 0.63 | 0.1719 | 1.0462375 | 0.80745 | 1.4037625 | 2.640957
1.18 | 2001 | 3326 | 3060 | -30 | 47 | -33 | 1.07 | 12.43 | 11.09 | 0 | 0.002 | 0000,00 0,00000 |  | 0.525 | 0.8225 | -0.175 | 0.1146 | 1.0523625 | 0.8124375 | 1.4039375 | 2.6423895
1.19 | 2004 | 3326 | 3062 | -40 | 10 | -11 | 1.07 | 12.44 | 10.98 | 0 | 0.003 | 0000,00 0,00000 |  | 0.7 | 0.175 | 0.21 | 0.1719 | 1.058575 | 0.8143625 | 1.4053375 | 2.643822
1.2 | 2006 | 3326 | 3060 | -31 | 12 | -19 | 1.08 | 12.45 | 10.77 | 0 | 0.002 | 0000,00 0,00000 |  | 0.5425 | 0.21 | 0.07 | 0.1146 | 1.0663625 | 0.8171625 | 1.40665 | 2.6452545
1.21 | 2002 | 3326 | 3062 | -58 | 20 | -12 | 1.08 | 12.46 | 10.83 | 0 | 0.003 | 0000,00 0,00000 |  | 1.015 | 0.35 | 0.1925 | 0.1719 | 1.07135 | 0.8196125 | 1.4063875 | 2.646687
1.22 | 2004 | 3326 | 3060 | 1 | 8 | -37 | 1.08 | 12.47 | 10.76 | 0 | 0.002 | 0000,00 0,00000 |  | -0.0175 | 0.14 | -0.245 | 0.1146 | 1.0728375 | 0.8246 | 1.4042 | 2.6475465
1.23 | 2001 | 3326 | 3060 | -18 | 49 | -34 | 1.08 | 12.49 | 10.88 | 0 | 0.001 | 0000,00 0,00000 |  | 0.315 | 0.8575 | -0.1925 | 0.0573 | 1.077475 | 0.8309 | 1.4044625 | 2.648406
1.24 | 2003 | 3326 | 3060 | -35 | 23 | -9 | 1.08 | 12.51 | 10.86 | 0 | 0.002 | 0000,00 0,00000 |  | 0.6125 | 0.4025 | 0.245 | 0.1146 | 1.0829875 | 0.8332625 | 1.4034125 | 2.648979
1.25 | 1999 | 3326 | 3062 | -28 | 4 | -49 | 1.09 | 12.53 | 11.07 | 0 | 0 | 0000,00 0,00000 |  | 0.49 | 0.07 | -0.455 | 0 | 1.0871 | 0.83685 | 1.4021 | 2.6492655
1.26 | 2001 | 3325 | 3062 | -19 | 37 | -12 | 1.17 | 12.61 | 11.12 | 0 | 0.001 | 0000,00 0,00000 |  | 0.3325 | 0.6475 | 0.1925 | 0.0573 | 1.092875 | 0.841925 | 1.4020125 | 2.649552
1.27 | 1999 | 3326 | 3060 | -47 | 21 | -35 | 1.17 | 12.63 | 11.28 | 0 | 0 | 0000,00 0,00000 |  | 0.8225 | 0.3675 | -0.21 | 0 | 1.097775 | 0.8460375 | 1.40315 | 2.6498385
1.28 | 2005 | 3326 | 3062 | -9 | 26 | 2 | 1.17 | 12.64 | 11.08 | 0 | 0.001 | 0000,00 0,00000 |  | 0.1575 | 0.455 | 0.4375 | 0.0573 | 1.1031125 | 0.8528625 | 1.40665 | 2.650698
1.29 | 1999 | 3326 | 3061 | -52 | 52 | -8 | 1.17 | 12.66 | 11.24 | 0 | 0.002 | 0000,00 0,00000 |  | 0.91 | 0.91 | 0.2625 | 0.1146 | 1.1109875 | 0.859425 | 1.40945 | 2.651844
1.3 | 2000 | 3326 | 3061 | -38 | 23 | -6 | 1.17 | 12.67 | 11.32 | 0 | 0.002 | 0000,00 0,00000 |  | 0.665 | 0.4025 | 0.2975 | 0.1146 | 1.1178125 | 0.8633625 | 1.4114625 | 2.6532765
1.31 | 1998 | 3326 | 3061 | -40 | 22 | -17 | 1.17 | 12.7 | 11.5 | 0 | 0.003 | 0000,00 0,00000 |  | 0.7 | 0.385 | 0.105 | 0.1719 | 1.1244625 | 0.8677375 | 1.4125125 | 2.6549955
1.32 | 1993 | 3325 | 3062 | -36 | 28 | -17 | 1.25 | 12.8 | 11.93 | 0 | 0.003 | 0000,00 0,00000 |  | 0.63 | 0.49 | 0.105 | 0.1719 | 1.130675 | 0.871325 | 1.4132125 | 2.6567145
1.33 | 2002 | 3325 | 3061 | -35 | 13 | -21 | 1.33 | 12.87 | 11.77 | 0 | 0.003 | 0000,00 0,00000 |  | 0.6125 | 0.2275 | 0.035 | 0.1719 | 1.13645 | 0.8764 | 1.4147 | 2.6584335
1.34 | 2002 | 3326 | 3060 | -31 | 45 | -8 | 1.33 | 12.88 | 11.64 | 0 | 0.003 | 0000,00 0,00000 |  | 0.5425 | 0.7875 | 0.2625 | 0.1719 | 1.1419625 | 0.8813875 | 1.4174125 | 2.660439
1.35 | 2005 | 3326 | 3060 | -32 | 12 | -7 | 1.32 | 12.88 | 11.36 | 0 | 0.004 | 0000,00 0,00000 |  | 0.56 | 0.21 | 0.28 | 0.2292 | 1.1500125 | 0.883925 | 1.419425 | 2.662731
1.36 | 2002 | 3324 | 3062 | -60 | 17 | -16 | 1.48 | 13.01 | 11.31 | 0 | 0.004 | 0000,00 0,00000 |  | 1.05 | 0.2975 | 0.1225 | 0.2292 | 1.1587625 | 0.8876 | 1.4196875 | 2.6647365
1.37 | 2003 | 3326 | 3062 | -40 | 25 | -27 | 1.47 | 13.01 | 11.21 | 0 | 0.003 | 0000,00 0,00000 |  | 0.7 | 0.4375 | -0.07 | 0.1719 | 1.164625 | 0.8925875 | 1.4212625 | 2.666742
1.38 | 2000 | 3325 | 3060 | -27 | 32 | -1 | 1.54 | 13.09 | 11.3 | 0 | 0.004 | 0000,00 0,00000 |  | 0.4725 | 0.56 | 0.385 | 0.2292 | 1.170575 | 0.89845 | 1.422225 | 2.6687475
1.39 | 1999 | 3326 | 3062 | -41 | 35 | -34 | 1.53 | 13.1 | 11.42 | 0 | 0.003 | 0000,00 0,00000 |  | 0.7175 | 0.6125 | -0.1925 | 0.1719 | 1.1753 | 0.9015125 | 1.422575 | 2.670753
1.4 | 2005 | 3326 | 3060 | -13 | 0 | -8 | 1.52 | 13.09 | 11.19 | 0 | 0.004 | 0000,00 0,00000 |  | 0.2275 | 0 | 0.2625 | 0.2292 | 1.17845 | 0.903875 | 1.4242375 | 2.673045
1.41 | 2002 | 3327 | 3062 | -23 | 27 | -19 | 1.44 | 13.03 | 11.17 | 0 | 0.004 | 0000,00 0,00000 |  | 0.4025 | 0.4725 | 0.07 | 0.2292 | 1.182475 | 0.9079875 | 1.4217875 | 2.674764
1.42 | 2001 | 3326 | 3062 | -23 | 20 | -55 | 1.43 | 13.04 | 11.21 | 0 | 0.002 | 0000,00 0,00000 |  | 0.4025 | 0.35 | -0.56 | 0.1146 | 1.1862375 | 0.9125375 | 1.41995 | 2.6761965
1.43 | 1999 | 3326 | 3062 | -20 | 32 | -12 | 1.43 | 13.06 | 11.35 | 0 | 0.003 | 0000,00 0,00000 |  | 0.35 | 0.56 | 0.1925 | 0.1719 | 1.1907 | 0.9177 | 1.4228375 | 2.6779155
1.44 | 2002 | 3326 | 3061 | -31 | 27 | -1 | 1.42 | 13.06 | 11.3 | 0 | 0.003 | 0000,00 0,00000 |  | 0.5425 | 0.4725 | 0.385 | 0.1719 | 1.197 | 0.922775 | 1.425025 | 2.6796345
1.45 | 2003 | 3326 | 3062 | -41 | 31 | -20 | 1.42 | 13.07 | 11.2 | 0 | 0.003 | 0000,00 0,00000 |  | 0.7175 | 0.5425 | 0.0525 | 0.1719 | 1.2033875 | 0.9258375 | 1.4258125 | 2.6813535
1.46 | 2005 | 3326 | 3062 | -32 | 4 | -17 | 1.41 | 13.06 | 11.01 | 0 | 0.003 | 0000,00 0,00000 |  | 0.56 | 0.07 | 0.105 | 0.1719 | 1.2088125 | 0.928025 | 1.4273875 | 2.683359
1.47 | 2001 | 3326 | 3062 | -30 | 21 | -11 | 1.41 | 13.07 | 11.08 | 0 | 0.004 | 0000,00 0,00000 |  | 0.525 | 0.3675 | 0.21 | 0.2292 | 1.2154625 | 0.930825 | 1.4293125 | 2.685651
1.48 | 2005 | 3326 | 3061 | -46 | 11 | -13 | 1.4 | 13.07 | 10.91 | 0 | 0.004 | 0000,00 0,00000 |  | 0.805 | 0.1925 | 0.175 | 0.2292 | 1.220275 | 0.9342375 | 1.42905 | 2.6876565
1.49 | 1998 | 3326 | 3060 | -9 | 28 | -36 | 1.4 | 13.09 | 11.16 | 0 | 0.003 | 0000,00 0,00000 |  | 0.1575 | 0.49 | -0.2275 | 0.1719 | 1.22535 | 0.939925 | 1.42695 | 2.6893755
1.5 | 2002 | 3326 | 3061 | -49 | 37 | -34 | 1.39 | 13.09 | 11.15 | 0 | 0.003 | 0000,00 0,00000 |  | 0.8575 | 0.6475 | -0.1925 | 0.1719 | 1.2313875 | 0.9443 | 1.4277375 | 2.6910945
1.51 | 2002 | 3326 | 3061 | -20 | 13 | -3 | 1.39 | 13.1 | 11.13 | 0 | 0.003 | 0000,00 0,00000 |  | 0.35 | 0.2275 | 0.35 | 0.1719 | 1.234975 | 0.949025 | 1.4301875 | 2.6928135
1.52 | 2001 | 3326 | 3060 | -21 | 41 | -15 | 1.39 | 13.11 | 11.18 | 0 | 0.003 | 0000,00 0,00000 |  | 0.3675 | 0.7175 | 0.14 | 0.1719 | 1.2408375 | 0.9554125 | 1.4287875 | 2.694246
1.53 | 2005 | 3325 | 3060 | -46 | 32 | -47 | 1.46 | 13.17 | 10.99 | 0 | 0.002 | 0000,00 0,00000 |  | 0.805 | 0.56 | -0.42 | 0.1146 | 1.2480125 | 0.9580375 | 1.426775 | 2.695392
1.54 | 2000 | 3326 | 3060 | -36 | -2 | -22 | 1.46 | 13.18 | 11.12 | 0 | 0.002 | 0000,00 0,00000 |  | 0.63 | -0.035 | 0.0175 | 0.1146 | 1.2551875 | 0.959175 | 1.4268625 | 2.696538
1.55 | 2005 | 3325 | 3062 | -46 | 15 | -23 | 1.53 | 13.24 | 10.94 | 0 | 0.002 | 0000,00 0,00000 |  | 0.805 | 0.2625 | 0 | 0.1146 | 1.2613125 | 0.961975 | 1.428525 | 2.6979705
1.56 | 2002 | 3325 | 3060 | -24 | 17 | -4 | 1.6 | 13.3 | 10.97 | 0 | 0.003 | 0000,00 0,00000 |  | 0.42 | 0.2975 | 0.3325 | 0.1719 | 1.2658625 | 0.96495 | 1.4319375 | 2.699976
1.57 | 2000 | 3326 | 3061 | -28 | 17 | -3 | 1.6 | 13.31 | 11.1 | 0 | 0.004 | 0000,00 0,00000 |  | 0.49 | 0.2975 | 0.35 | 0.2292 | 1.27085 | 0.96775 | 1.4350875 | 2.702268
1.58 | 2003 | 3326 | 3061 | -29 | 15 | -7 | 1.59 | 13.31 | 11.04 | 0 | 0.004 | 0000,00 0,00000 |  | 0.5075 | 0.2625 | 0.28 | 0.2292 | 1.2740875 | 0.97125 | 1.43465 | 2.7042735
1.59 | 2003 | 3326 | 3062 | -8 | 25 | -44 | 1.58 | 13.31 | 10.99 | 0 | 0.003 | 0000,00 0,00000 |  | 0.14 | 0.4375 | -0.3675 | 0.1719 | 1.27855 | 0.97545 | 1.4315 | 2.705706
1.6 | 2008 | 3326 | 3062 | -43 | 23 | -38 | 1.57 | 13.29 | 10.67 | 0 | 0.002 | 0000,00 0,00000 |  | 0.7525 | 0.4025 | -0.2625 | 0.1146 | 1.2847625 | 0.9769375 | 1.4107625 | 2.7042735
1.61 | 1998 | 3326 | 3060 | -28 | -6 | -245 | 1.56 | 13.3 | 10.97 | 0 | -0.007 | 0000,00 0,00000 |  | 0.49 | -0.105 | -3.885 | -0.4011 | 1.29045 | 0.9772875 | 1.3918625 | 2.700549
1.62 | 2006 | 3326 | 3062 | -37 | 10 | -17 | 1.55 | 13.29 | 10.77 | 0 | -0.006 | 0000,00 0,00000 |  | 0.6475 | 0.175 | 0.105 | -0.3438 | 1.296925 | 0.9814875 | 1.3922125 | 2.6973975
1.63 | 2005 | 3326 | 3061 | -37 | 38 | -25 | 1.54 | 13.29 | 10.66 | 0 | -0.005 | 0000,00 0,00000 |  | 0.6475 | 0.665 | -0.035 | -0.2865 | 1.3054125 | 0.9860375 | 1.3909875 | 2.6945325
1.64 | 2006 | 3326 | 3062 | -60 | 14 | -35 | 1.54 | 13.28 | 10.51 | 0 | -0.005 | 0000,00 0,00000 |  | 1.05 | 0.245 | -0.21 | -0.2865 | 1.3132 | 0.9870875 | 1.3899375 | 2.6916675
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

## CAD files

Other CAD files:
RocketDrawings/Alette.3dm
RocketDrawings/Copritelecamera.3dm
RocketDrawings/Intruder esploso.3dm
RocketDrawings/Intruder separato.3dm
RocketDrawings/Intruder tesi.3dm
RocketDrawings/Schema variazione alfa in rollio.3dm

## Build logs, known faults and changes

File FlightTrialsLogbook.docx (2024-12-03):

# Diario delle prove sperimentali per la tesi magistale

Castelvetrano 09 Feb 2012

Settaggi comuni ai due voli: taratura del giroscopio P0=-29 Q0 =+19 R0=-30 Servo zero=1,4ms KalmAlt main=130m Gwiz main=115m.

- Volo 1) Volo con alette fisse a 0°. Volo da manuale, presente un forte spin di circa 1 giro al secondo in senso negativo.

- Volo 2) Colo con alette fisse a +7=. Volo OK. All'apertura del main una sua funicella si è incagliata nell'aletta ma non ci sono state conseguenze. Il rollio sembra rimasto uguale nel suo valore massimo ma dura più a lungo.

Considerazioni scaturite dall'analisi

1. Il sistema di controllo rileva il lancio troppo tardi, quindi si perdono i primissimi istanti di volo. Meglio utilizzare come criterio che l'accelerazione relativa, così come misurata dal kalman a bordo, sia >= 25 m/s^2
2. P0, Q0 ed R0, che si supponevano essere costanti per dato esemplare di giroscopio, invece variano. Bisogna implementare una taratura automatica all'accensione del sistema.
3. Per trovare l'effettiva traiettoria del razzo bisogna cambiare sistema di riferimento.
4. Le alette sembrano controllare poco. Necessario investigare ulteriormente.
5. La dinamica del filtro di Kalman per il rollio è troppo lenta.
6. L'asimmetricità della carenatura della telecamera provoca un angolo di side-slip che probabilmente influenza il rollio.
7. L'ugello in grafite si usura parecchio. Ciò potrebbe portare ad asimmetrie nella spinta.

Modifiche apportate dopo questa giornata di lanci

1. Creata una carenatura della telecamera uguale che è stata posta simmetricamente alla prima. Inoltre le carenature sono state allineate al piano di simmetria del razzo (XZ).
2. Creata la taratura automatica di P0 Q0 R0 all'accensione.
3. Implementato il nuovo criterio di rilevazione del lancio.
4. Implementato un nuovo programma che prevede una manovra delle alette appena il razzo rallenta sotto i 55 m/s.
5. Creato un ugello in acciaio per scongiurare il pericolo di asimmetrie nella spinta.

Castelvetrano 01 Mar 2012

Settaggi comuni ai due voli: P0, Q0 ed R0 si tarano da soli all'accensione. Servo zero = ? KalmAlt main=130m Gwiz main=115m

- Volo 1) Volo con alette fisse a 0°. S Volo ottimo. Il razzo ha oscillato un poco per il vento in uscita dalla rampa, presente una velocità di rollio di circa 500°/s in senso negativo.

- Volo 2) Volo con manovra delle alette: alette ruotate a +9° finché il razzo non ha rallentato sotto i 55 m/s, poi le alette sono passate istantaneamente a -9°. L'ascesa è andata bene, ma quando si è attivato il sistema di sgancio del paracadute principale, questo ha impiegato molto tempo a dispiegarsi. ~~Il problema è stato causato probabilmente dall'eccessiva rigidezza del cavo i uno dei due accenditori.~~ L'atterraggio è sfortunatamente avvenuto sull'asfalto. L'impatto ha danneggiato l'accoppiatore, un'aletta di coda e ha ruotato un'aletta di controllo facendo slittare l'asse nello strozza albero.

Considerazioni scaturite dall'analisi

1. Necessario paracadute più grande per ridurre ulteriormente la velocità di atterraggio.
2. Bisogna trovare un modo per fare aprire in maniera più sicura il paracadute principale.
3. Le alette controllano bene se tendono a contrastare il rollio, male a favorirlo. Investigare.
4. Le alette di controllo devono essere ingrandite perché, anche alla massima deflessione (9°), non riescono a contrastare completamente il rollio.

Castelvetrano 29 Marzo 2012

Settaggi volo 1: P0, Q0 ed R0 si tarano da soli all'accensione. Servo zero = ? KalmAlt main=130m Gwiz main=115m. Montate le alette grandi

Settaggi volo 2: P0, Q0 ed R0 si tarano da soli all'accensione. Servo zero = ? KalmAlt main=200m Gwiz main=115m. Montate le alette piccole

- Volo 1) Controllo del rollio attivo. Volo andato male: durante i primi istanti di volo si è rotto a flessione uno dei due assi delle alette canard e il modello ha cominciato a sbandare copiosamente rollando su se stesso. C'è una mutua rotazione tra le sezioni del razzo.

- Volo 2) Controllo del rollio attivo e alette piccole montate. Volo buono, il sistema di controllo ha funzionato bene. Anche in questo volo c'è una rotazione mutua tra le sezioni del razzo. Questo difetto però non ha comportato gravi problemi a parte un disturbo aggiuntivo che il sistema è riuscito ad attenuare decentemente. Il paracadute principale si è incastrato nelle alette, tuttavia non si sono riscontrate conseguenze.

Considerazioni scaturite dall'analisi

1. Nel primo volo l'asse si è rotto perché la parte del raccordo asse-aletta aveva la parte cilindrica che si infila dentro l'asse troppo corta, dunque a beccarsi lo sforzo è stato solo l'asse in carbonio.

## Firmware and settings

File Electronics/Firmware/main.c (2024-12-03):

/********************************************************************
 FileName:      main.c
 Dependencies:  See INCLUDES section
 Processor:		PIC18F2553
 Hardware:		Mio
 Complier:  	Microchip C18
 Owner:         Adriano Arcadipane
********************************************************************/
#ifndef MAIN_C
#define MAIN_C

/** INCLUDES *******************************************************/
#include "Strutture_e_prototipi.h"

//*************CONFIGURATION*****************************************
        #pragma config PLLDIV   = 2           // (8 MHz crystal)
        #pragma config CPUDIV   = OSC1_PLL2   //[Primary Oscillator Src: /2][96 MHz PLL Src: /3] 
        #pragma config USBDIV   = 2           // Clock source from 96MHz PLL/2
        #pragma config FOSC     = HSPLL_HS
        #pragma config FCMEN    = OFF
        #pragma config IESO     = OFF
        #pragma config PWRT     = OFF
        #pragma config BOR      = ON
        #pragma config BORV     = 3
        #pragma config VREGEN   = ON           //USB Voltage Regulator
        #pragma config WDT      = OFF
        #pragma config WDTPS    = 32768
        #pragma config MCLRE    = ON
        #pragma config LPT1OSC  = OFF
        #pragma config PBADEN   = OFF          //PORTB 4:0 are digital I/O
//      #pragma config CCP2MX   = ON
        #pragma config STVREN   = ON
        #pragma config LVP      = OFF
//      #pragma config ICPRT    = OFF          // Dedicated In-Circuit Debug/Programming
        #pragma config XINST    = OFF          // Extended Instruction Set
        #pragma config CP0      = OFF
        #pragma config CP1      = OFF
//      #pragma config CP2      = OFF
//      #pragma config CP3      = OFF
        #pragma config CPB      = OFF
//      #pragma config CPD      = OFF
        #pragma config WRT0     = OFF
        #pragma config WRT1     = OFF
//      #pragma config WRT2     = OFF
//      #pragma config WRT3     = OFF
        #pragma config WRTB     = OFF          // Boot Block Write Protection
        #pragma config WRTC     = OFF
//      #pragma config WRTD     = OFF
        #pragma config EBTR0    = OFF
        #pragma config EBTR1    = OFF
//      #pragma config EBTR2    = OFF
//      #pragma config EBTR3    = OFF
        #pragma config EBTRB    = OFF

/** GLOBAL VARIABLES ******************************************************/
//VARIABILI PER LA USB
#pragma udata
#pragma udata USB_VARIABLES=0x500
unsigned char ReceivedDataBuffer[64];
unsigned char ToSendDataBuffer[64];
#pragma code
#pragma udata

//VARIABILI NORMALI
USB_HANDLE USBOutHandle = 0;
USB_HANDLE USBInHandle = 0;
BOOL blinkStatusValid = TRUE;

unsigned char pwm_state = 0;
unsigned int pwm_alto,         
             pwm_basso;
StrValoriPWM PWM;           //Dichiaro PWM come variabile di tipo ValoriPWM...

/** PRIVATE PROTOTYPES *********************************************/
static void InitializeSystem(void);
void ProcessIO(void);
void YourHighPriorityISRCode();
void YourLowPriorityISRCode();
void USBCBSendResume(void);
void Principale(void);
void gestione_errori (unsigned char);
void azzera_ToSendDataBuffer(void);

/** VARIABILI ESTERNE **********************************************/

#include "VectorRemapping.h"     //Rimappatura ISV in caso di bootloader

/**ROUTINE DI INTERRUPT*********************************************/
#pragma code
	//These are your actual interrupt handling routines.
	#pragma interrupt YourHighPriorityISRCode
	void YourHighPriorityISRCode()
	{
        if (PIR1bits.TMR1IF) {        //Overflow del timer1 (PWM)
            if (pwm_state == 0){
                SERVO = 1;
                pwm_state = 1;
                WriteTimer1(pwm_alto);
            }
            else {
                SERVO = 0;
                pwm_state = 0;
                WriteTimer1(pwm_basso);
            }
        PIR1bits.TMR1IF = 0;
        }

		//Check which interrupt flag caused the interrupt.
		//Service the interrupt
		//Clear the interrupt flag
		//Etc.
        if (PIR2bits.USBIF){
        #if defined(USB_INTERRUPT)
	        USBDeviceTasks();
        #endif
        }
	}//This return will be a "retfie fast", since this is in a #pragma interrupt section 

	#pragma interruptlow YourLowPriorityISRCode
	void YourLowPriorityISRCode()
	{
		//Check which interrupt flag caused the interrupt.
		//Service the interrupt
		//Clear the interrupt flag
		//Etc.
	
	}	//This return will be a "retfie", since this is in a #pragma interruptlow section 
#endif

/** DECLARATIONS ***************************************************/
#pragma code


// * Function:        void main(void)
//********************************************************************
void main(void){   

    InitializeSystem();  //Inizializza il sistema
    delay_ms(150);       //Pausa per stabilizzare i sistemi
    
//Se la porta USB non è connessa all'accensione il sistema esegue
//la parte principale del programma
    if (PORTCbits.RC6 == 0) {
        Principale();           //Contenuta in CorpoProgramma.c
    }
//Altrimenti passa alla programma di comunicazione
    USBDeviceAttach(); 
    PIE1bits.TMR1IE = 1;     //Disabilita l'interrupt per il timer 1
    
    while(1)
    {
		// Application-specific tasks.
		// Application related code may be added here, or in the ProcessIO() function.
        ProcessIO();        
    }//end while
}//end main


/********************************************************************
 * Function:        static void InitializeSystem(void)
 * PreCondition:    None
 * Input:           None
 * Output:          None
 * Side Effects:    None
 * Overview:        InitializeSystem is a centralize initialization
 *                  routine. All required USB initialization routines
 *                  are called from here.
 *
 *                  User application initialization routine should
 *                  also be called from here.                  
 *
 * Note:            None
 *******************************************************************/
static void InitializeSystem(void){

    //Setto il clock per la libreria delay
    setQuartz (48);

    //Pins
    //La selezione dei canali come analogici o digitali verrà fatta
    //tramite la libreria ADC
    PORTA = 0b0000000;    //Tutte le porte basse
    PORTB = 0b0000000;   
    PORTC = 0b0000000;
    PORTE = 0b0000000;

    TRISA = 0b11111111;          //PORTA A tutti ingressi (ci sono i canali analogici)
    TRISB = 0b0000001;           //Tutte le porte B sono uscite tranne lo SPI IN
    TRISCbits.TRISC7 = OUTPUT;    //Lo SPI out è un'uscita
    TRISCbits.TRISC6 = INPUT;    //L'USB sense è input
    TRISCbits.TRISC0 = OUTPUT;   //Led è un uscita
    TRISCbits.TRISC2 = OUTPUT;   //Il servo è un uscita
    
    
    //SPI
    OpenSPI(SPI_FOSC_16,MODE_00,SMPEND);   //Attiva e configura la SPI a 3MHz
    CS_MEMORIA = 1;                        //Tutti i chip select sono alti
    CS_GYRO = 1;
    CS_AUX = 1;    

    //ADC
    OpenADC(ADC_FOSC_16 & ADC_RIGHT_JUST & ADC_20_TAD,   //il 12 fa in modo che siano analogici solo
            ADC_CH2 & ADC_INT_OFF & ADC_VREFPLUS_VDD & ADC_VREFMINUS_VSS,   //i canali 0, 1, 2, 3
            11);


    //USB
    USBOutHandle = 0;
    USBInHandle = 0;  
    USBDeviceInit();	//usb_device.c.  Initializes USB module SFRs and firmware
    					//variables to known states. 

    //L3G4200 GYROSCOPE
      //Attiva il giroscopio settando il bit PD e seleziona DATA RATE e
      //il primo filtro passa basso 
    gyro_write_register(CTRL_REG1,0b10111111);  
      //Setta il filtro passa alto
    gyro_write_register(CTRL_REG2,0b00001000);
      //Setta la modalità BDU che blocca l'aggiornamento se non si è letto anche l'LSB
      //e seleziona il fondoscala di 500°/s
    gyro_write_register(CTRL_REG4,0b10010000);
      //Disattiva il filtro passa alto e attiva secondo il passa basso
    gyro_write_register(CTRL_REG5,0b00000011);
    
    
    //FRAM
    fram_write_register(0b11000000);   //Toglie le protezioni software inizializzando la FRAM
   

    //TIMERS
    //Timer0 per generare il clock di base per l'elaborazione e acquisizione
    OpenTimer0 (TIMER_INT_OFF   & //Interrupt disabled
                T0_16BIT        & //16-bit mode
                T0_SOURCE_INT   & //Internal clock source (TOSC)
                T0_EDGE_FALL    & //INUTILIZZATO External clock on falling edge
                T0_PS_1_2);       //1:2 prescale
    WriteTimer0 (TIMER0_START_VALUE);    //Azzera il timer al valore stabilito (vedi HardwareProfile)
    T0CONbits.TMR0ON = 0;             //Spegne il timer            

    //Timer1 per generare il PWM tramite continui interrupt
    OpenTimer1( TIMER_INT_OFF   & //Interrupt disabilitati, verranno abilitati al momento giusto
                T1_16BIT_RW     & //16-bit mode
                T1_SOURCE_INT   & //Internal clock source (TOSC)
                T1_PS_1_4       & //1:4 prescale
                T1_OSC1EN_OFF   & //Disable Timer1 oscillator
                T1_SYNC_EXT_OFF); //Don’t sync external clock input
    T1CONbits.TMR1ON = 0;             //Spegne il timer
    
    //INTERRUPT
    RCONbits.IPEN = 1;     //Priorità abilitate
    INTCONbits.GIEH = 0;   //Disabilita interrupt ad alta priorità, verranno attivati al momento opportuno
    INTCONbits.GIEL = 0;   //Disabilita interrupt a bassa priorità
    IPR1bits.TMR1IP = 1;   //L'overflow del Timer1 è ad alta priorità
    PIE1bits.TMR1IE = 1;   //Abilita l'interrupt da Timer1 per la generazione del PWM 
       
    INTCONbits.TMR0IF = 0; //Pulisce gli interrupt flag per i timer
    PIR1bits.TMR1IF = 0;   



    //EEPROM INTERNA
    if (readIntEEPROM (16) == 0xFF){    //Se la memoria interna è vergine, la riempie con i valori predefiniti
	                                     //Utilizza la cella di memoria 16 perchè è quella in cui è memorizzato
	                                     //il programma da eseguire, che mai sarà 255.
        unsigned char verifica = 0;     //Dichiara una variabile utile alla verifica della corretta scrittura
        
        //Vedere HardwareProfile.h per i valori
        //Se la scrittura riesce il risultato della funzione write è 1. Questo risultato
        //vine invertito per mezzo di ~ e sommato alla variabile di verifica. Se tutto
        //è andato bene alla fine verifica sarà zero.
        
        //Valori di taratura del giroscopio aboliti dalla versione 0.10
        //da ora in poi vengono impostati all'avvio.
        //verifica = verifica + !writeIntEEPROM ((char)(P0_SU_EEPROM >> 8),0);                     //zero rate level asse X giroscopio MSB
        //verifica = verifica + !writeIntEEPROM ((char) P0_SU_EEPROM,1);                           //"" LSB    
        //verifica = verifica + !writeIntEEPROM ((char)(Q0_SU_EEPROM >> 8),2);                     //zero rate level asse Y giroscopio MSB           
        //verifica = verifica + !writeIntEEPROM ((char) Q0_SU_EEPROM,3);                           //"" LSB    
        //verifica = verifica + !writeIntEEPROM ((char)(R0_SU_EEPROM >> 8),4);                     //zero rate level asse Y giroscopio MSB
        //verifica = verifica + !writeIntEEPROM ((char) R0_SU_EEPROM,5);                           //"" LSB     
        verifica = verifica + !writeIntEEPROM ((char)(LOW_BATTERY_VALUE_SU_EEPROM >> 8),6);      //MSB valore minimo batteria           
        verifica = verifica + !writeIntEEPROM ((char) LOW_BATTERY_VALUE_SU_EEPROM,7);            //LSB valore minimo batteria
        verifica = verifica + !writeIntEEPROM ((char)(SERVO_ZERO_SU_EEPROM >> 8),8);             //MSB posizione centrale servo
        verifica = verifica + !writeIntEEPROM ((char) SERVO_ZERO_SU_EEPROM,9);                   //LSB posizione centrale servo
        verifica = verifica + !writeIntEEPROM ((char)(MIN_ROTAZIONE_RAD_SU_EEPROM >> 8),10);  //MSB max posizione oraria servo
        verifica = verifica + !writeIntEEPROM ((char) MIN_ROTAZIONE_RAD_SU_EEPROM,11);        //LSB max posizione oraria servo
        verifica = verifica + !writeIntEEPROM ((char)(MAX_ROTAZIONE_RAD_SU_EEPROM >> 8),12);  //MSB max posizione antioraria servo
        verifica = verifica + !writeIntEEPROM ((char) MAX_ROTAZIONE_RAD_SU_EEPROM,13);        //LSB max posizione antioraria servo
        verifica = verifica + !writeIntEEPROM ((char)(T_TAU_DELTA_SU_EEPROM >> 8),14);        //MSB Trasferenza tra tempo pwm alto e rotazione alette
        verifica = verifica + !writeIntEEPROM ((char) T_TAU_DELTA_SU_EEPROM,15); 
        verifica = verifica + !writeIntEEPROM ((char) PROGRAMMA_SU_EEPROM,16);                        //Programma da eseguire
        verifica = verifica + !writeIntEEPROM ((char)(ROTAZIONE_PER_PROGRAMMA_1_SU_EEPROM >> 8),17);  //MSB rotazione in rad*10000 da mantenere durante il programma 1
        verifica = verifica + !writeIntEEPROM ((char) ROTAZIONE_PER_PROGRAMMA_1_SU_EEPROM,18);        //LSB rotazione in rad*10000 da mantenere durante il programma 1
        verifica = verifica + !writeIntEEPROM ((char) (KP_SU_EEPROM >> 8),19);                               //MSB azione proporzionale * 10000
        verifica = verifica + !writeIntEEPROM ((char) KP_SU_EEPROM,20);                               //LSB azione proporzionale * 10000   
        verifica = verifica + !writeIntEEPROM ((char) (KI_SU_EEPROM >> 8),21);                               //MSB azione Integrale * 10000
        verifica = verifica + !writeIntEEPROM ((char) KI_SU_EEPROM,22);                               //LSB azione Integrale * 10000         
        verifica = verifica + !writeIntEEPROM ((char) (KD_SU_EEPROM >> 8),23);                               //MSB azione derivativa * 10000
        verifica = verifica + !writeIntEEPROM ((char) KD_SU_EEPROM,24);                               //LSB azione derivativa * 10000         
        //Se "verifica" è diverso da zero chiama la routine di gestione errori con codice 1
        if (verifica != 0) gestione_errori(1);
    }//fine IF


    //ALTRO
    LED = 1;            //Accende il led

}//end InitializeSystem



/********************************************************************
 * Function:        void ProcessIO(void)
 * PreCondition:    None
 * Input:           None
 * Output:          None
 * Side Effects:    None
 * Overview:        This function is a place holder for other user
 *                  routines. It is a mixture of both USB and
 *                  non-USB tasks.
 *
 * Note:            None
 *******************************************************************/
void ProcessIO(void){
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

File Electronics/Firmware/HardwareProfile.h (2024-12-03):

/********************************************************************
 FileName:      HardwareProfile.h
 Dependencies:  See INCLUDES section
 Processor:		PIC18F2553
 Hardware:		Mio
 Complier:  	Microchip C18
 Owner:         Adriano Arcadipane

 In questo file .h si espleta la configurazione hardware
 assegnando le porte e la configurazione del sistema
*******************************************************************
 File Description:

********************************************************************/

#ifndef HARDWARE_PROFILE_H
#define HARDWARE_PROFILE_H


    /*******************************************************************/
    /******** USB stack hardware selection options *********************/
    /*******************************************************************/
    //This section is the set of definitions required by the MCHPFSUSB
    //  framework.  These definitions tell the firmware what mode it is
    //  running in, and where it can find the results to some information
    //  that the stack needs.
    //These definitions are required by every application developed with
    //  this revision of the MCHPFSUSB framework.  Please review each
    //  option carefully and determine which options are desired/required
    //  for your application.

    //The PICDEM FS USB Demo Board platform supports the USE_SELF_POWER_SENSE_IO
    //and USE_USB_BUS_SENSE_IO features.  Uncomment the below line(s) if
    //it is desireable to use one or both of the features.
    //#define USE_SELF_POWER_SENSE_IO
    //#define tris_self_power     TRISAbits.TRISA2    // Input
    #if defined(USE_SELF_POWER_SENSE_IO)
    #define self_power          PORTAbits.RA2
    #else
    #define self_power          1
    #endif

    //#define USE_USB_BUS_SENSE_IO
    //#define tris_usb_bus_sense  TRISAbits.TRISA1    // Input
    #if defined(USE_USB_BUS_SENSE_IO)
    #define USB_BUS_SENSE       PORTAbits.RA1
    #else
    #define USB_BUS_SENSE       1
    #endif


    //Uncomment the following line to make the output HEX of this  
    //  project work with the MCHPUSB Bootloader    
    //#define PROGRAMMABLE_WITH_USB_MCHPUSB_BOOTLOADER
	
    //Uncomment the following line to make the output HEX of this 
    //  project work with the HID Bootloader
    //#define PROGRAMMABLE_WITH_USB_HID_BOOTLOADER		

    /*******************************************************************/
    /*******************************************************************/
    /*******************************************************************/
    /******** Application specific definitions *************************/
    /*******************************************************************/
    /*******************************************************************/
    /*******************************************************************/

    /** Board definition ***********************************************/
    //These defintions will tell the main() function which board is
    //  currently selected.  This will allow the application to add
    //  the correct configuration bits as wells use the correct
    //  initialization functions for the board.  These defitions are only
    //  required in the stack provided demos.  They are not required in
    //  final application design.
    //#define DEMO_BOARD PICDEM_FS_USB
    //#define PICDEM_FS_USB
    //#define CLOCK_FREQ 48000000


    /** ASSEGNAZIONE PIN **********************************************/
 //   #define mInitAllLEDs()      LATB &= 0xF0; TRISB &= 0xF0;
       
    #define CS_MEMORIA          PORTBbits.RB2   //CS per la memoria, il giroscopio e per il canale ausiliario
    #define CS_GYRO             PORTBbits.RB3
    #define CS_AUX              PORTBbits.RB4
    #define BUZZER              PORTBbits.RB5
    #define LED                 PORTCbits.RC0
    #define ANALOG_AUX          ADC_CH0         //canali analogici 
    #define ACCELEROMETRO       ADC_CH1
    #define BAROMETRO           ADC_CH2
    #define BATTERIA            ADC_CH3
    #define SERVO               PORTCbits.RC2   //Uscita servo
  
    /** I/O pin definitions ********************************************/
    #define INPUT 1       //Così è più facile ricordare tutta la storia
    #define OUTPUT 0

    #define HIBYTE(i)   ((unsigned char)(((int)(i)) >> 8))
    #define LOBYTE(i)   ((unsigned char)(((int)(i)) & 0xFF))
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
